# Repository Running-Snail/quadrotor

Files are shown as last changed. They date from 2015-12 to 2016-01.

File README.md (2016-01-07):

# Quadrotor
迷你四旋翼

## steps
1. 用nano板接电机，接MOFSET管，接3.7v电压，PWM测试
    1. 测试用MOFSET管（把面包线焊到三个引脚上）√ 3.7v下转动 1.13A N沟道
    2. 编写一路测试PWM（程序硬编码一个特定的百分比值）√
    3. 电池测试 √
2. 测试多路PWM和空心杯驱动（与下一步画电路板同时进行）
    1. 4路PWM驱动电机测试
    2. 电池驱动测试
    3. 蓝牙通讯（制定协议√，电脑或者手机端蓝牙传输通讯）
    4. 蓝牙协议，avr端实现 √
    5. avr端实现优化
    6. 蓝牙协议，android端实现
3. 画电路板（测试板，开发板）
    1. 初步电路√，万用板搭建实验
    2. 购买芯片（估计要买很多，以供下面的步骤使用）
    3. 焊接芯片
    4. 调试 -> 改正
4. 四旋翼结构设计
    1. 程序模拟（这个不太了解怎么模拟）
    2. 做一个模型进行测试
5. 画正式四旋翼电路板
    1. 焊接芯片
    2. 调试 -> 改正

## 蓝牙协议
接收bytes序列
序列格式

```
| pkg byte | pkg byte2 (optional) | ... | data len byte ( use 7 bits ) | data len byte 2 (optional) | ... | actual data | xor check sum |
```

```
pkgs
HELLO 0x48
SET_MOTOR 0x53
FEEDBACK 0x41
ERROR 0x45 
```

```
ERROR types
buffer_overflow 0x1
```

### SET_MOTOR 设置电机转速
设置电机1的转速为128

```
| 0x53 | 0x02 | 0x00 | 0x80 | 0xd1 |
```

### HELLO 包
```
| 0x48 | 0x0 | 0x48 | 
```

### OK 回执
```
| 0x41 | 0x2 | 0x6f | 0x6b | 0x47 |
```

## notes
* 720空心杯3.7v电压下转动 电流测得1.13A
* 笔记本usb的电流不够大，空心杯转起来了之后就没有额外的电流提供给蓝牙模块了，使用锂电池解决这个问题
* 电机转速太快的情况下会对蓝牙模块产生电磁干扰（怀疑，还需证实，需要在电机壳上加电容）
* 电路原理图
    * atmega328p最小系统
        * 晶振电路 √
        * reset按键 √
        * 电源开关 电源灯 电源插头 √
        * 稳压电路 √
        * 滤波电容 √
        * 编程/运行开关 √
        * 编程接口 √
            * 使用arduino的bootloader
                * usb转串口 外置 留出RX TX 
            * SPI下载接口 √
    * 电机电路
        * 四路PWM N沟道 MOSFET电路 √
        * 电机及外壳电容电路（减弱磁场效应）
    * 通讯模块
        * 蓝牙模块接口 √
    * 电池固定结构

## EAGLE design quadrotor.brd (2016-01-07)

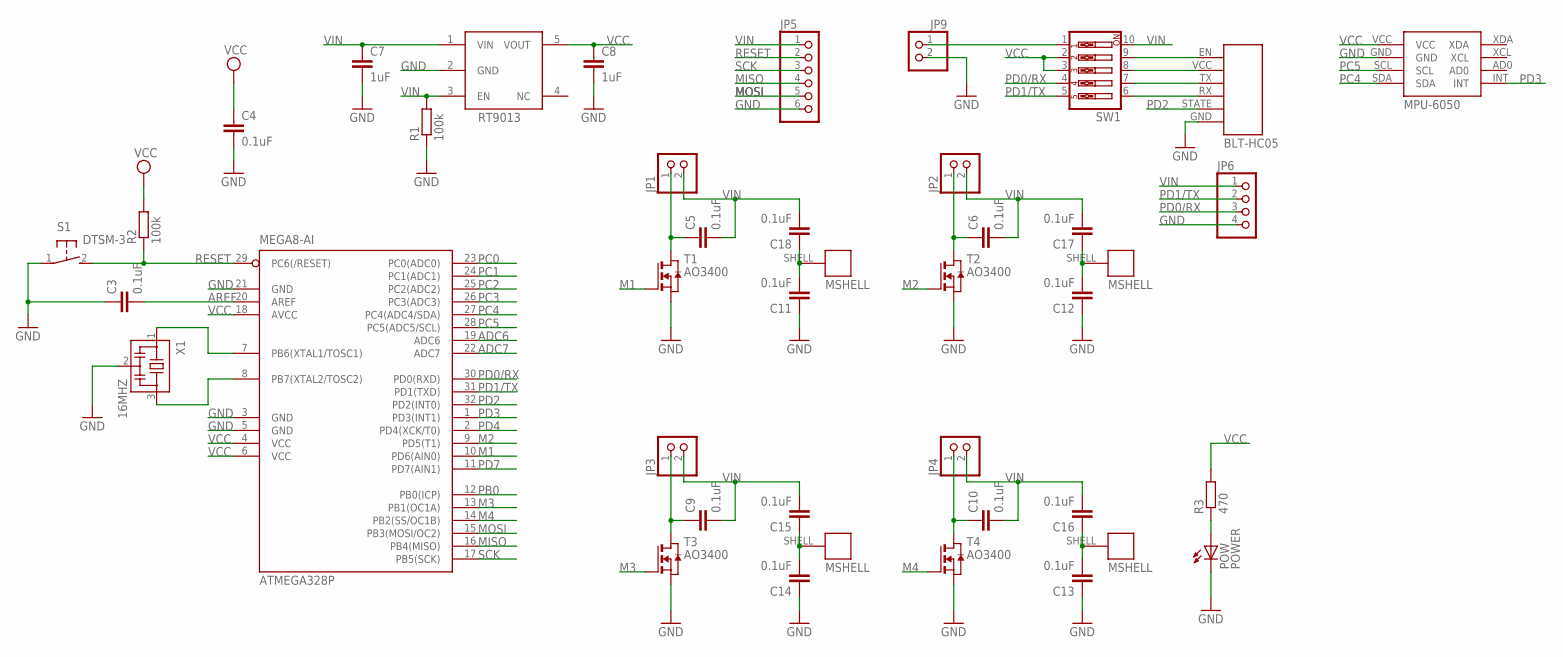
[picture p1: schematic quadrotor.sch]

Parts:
ATMEGA328P: MEGA8-AI; TQFP32-08
C3, C4, C5, C6, C9, C10, C11, C12, C13, C14, C15, C16, C17, C18: 0.1uF; C0603
C7, C8: 1uF; C0603
JP1, JP2, JP3, JP4, JP9: PINHD-1X2; 1X02
JP5: PINHD-1X6; 1X06
JP6: PINHD-1X4; 1X04
POW: POWER; LED_SML0603
R1, R2: 100k; R0603
R3: 470; R0603
S1: DTSM-3
SW1: SW_DIP-5; EDG-05
T1, T2, T3, T4: AO3400; SOT-23
U$1: RT9013; SOT-23-5
U$2: BLT-HC05
U$3, U$4, U$5, U$6: 720-MSHELL; 720MOTOR
U$7: MPU-6050
X1: 16MHZ; CSTCR6M

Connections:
ADC6: ATMEGA328P.19 (ADC6)
ADC7: ATMEGA328P.22 (ADC7)
AREF: ATMEGA328P.20 (AREF), C3.2
GND: ATMEGA328P.3 (GND), ATMEGA328P.5 (GND), ATMEGA328P.21 (GND), C3.1, C4.2, C7.2, C8.2, C11.1, C12.1, C13.1, C14.1, JP5.6, JP6.4, JP9.2, POW.C, R1.1, S1.1, T1.2 (S), T2.2 (S), T3.2 (S), T4.2 (S), U$1.2 (GND), U$2.GND, U$7.GND, X1.2
M1: ATMEGA328P.10 (PD6(AIN0)), T1.3 (G)
M2: ATMEGA328P.9 (PD5(T1)), T2.3 (G)
M3: ATMEGA328P.13 (PB1(OC1A)), T3.3 (G)
M4: ATMEGA328P.14 (PB2(SS/OC1B)), T4.3 (G)
MISO: ATMEGA328P.16 (PB4(MISO)), JP5.4
MOSI: ATMEGA328P.15 (PB3(MOSI/OC2)), JP5.5
unnamed: ATMEGA328P.7 (PB6(XTAL1/TOSC1)), X1.1
unnamed: ATMEGA328P.8 (PB7(XTAL2/TOSC2)), X1.3
unnamed: C14.2, C15.1, U$5.SHELL
unnamed: C5.1, JP1.1, T1.1 (D)
unnamed: C11.2, C18.1, U$3.SHELL
unnamed: C6.1, JP2.1, T2.1 (D)
unnamed: SW1.9, U$2.EN
unnamed: POW.A, R3.1
unnamed: C10.1, JP4.1, T4.1 (D)
unnamed: C9.1, JP3.1, T3.1 (D)
unnamed: SW1.8, U$2.VCC
unnamed: SW1.7, U$2.TX
unnamed: SW1.6, U$2.RX
unnamed: JP9.1, SW1.1
unnamed: C12.2, C17.1, U$4.SHELL
unnamed: C13.2, C16.1, U$6.SHELL
PB0: ATMEGA328P.12 (PB0(ICP))
PC0: ATMEGA328P.23 (PC0(ADC0))
PC1: ATMEGA328P.24 (PC1(ADC1))
PC2: ATMEGA328P.25 (PC2(ADC2))
PC3: ATMEGA328P.26 (PC3(ADC3))
PC4: ATMEGA328P.27 (PC4(ADC4/SDA)), U$7.SDA
PC5: ATMEGA328P.28 (PC5(ADC5/SCL)), U$7.SCL
PD0/RX: ATMEGA328P.30 (PD0(RXD)), JP6.3, SW1.4
PD1/TX: ATMEGA328P.31 (PD1(TXD)), JP6.2, SW1.5
PD2: ATMEGA328P.32 (PD2(INT0)), U$2.STATE
PD3: ATMEGA328P.1 (PD3(INT1)), U$7.INT
PD4: ATMEGA328P.2 (PD4(XCK/T0))
PD7: ATMEGA328P.11 (PD7(AIN1))
RESET: ATMEGA328P.29 (PC6(/RESET)), JP5.2, R2.1, S1.2
SCK: ATMEGA328P.17 (PB5(SCK)), JP5.3
VCC: ATMEGA328P.4 (VCC), ATMEGA328P.6 (VCC), ATMEGA328P.18 (AVCC), C4.1, C8.1, R2.2, R3.2, SW1.2, SW1.3, U$1.5 (VOUT), U$7.VCC
VIN: C5.2, C6.2, C7.1, C9.2, C10.2, C15.2, C16.2, C17.2, C18.2, JP1.2, JP2.2, JP3.2, JP4.2, JP5.1, JP6.1, R1.2, SW1.10, U$1.1 (VIN), U$1.3 (EN)

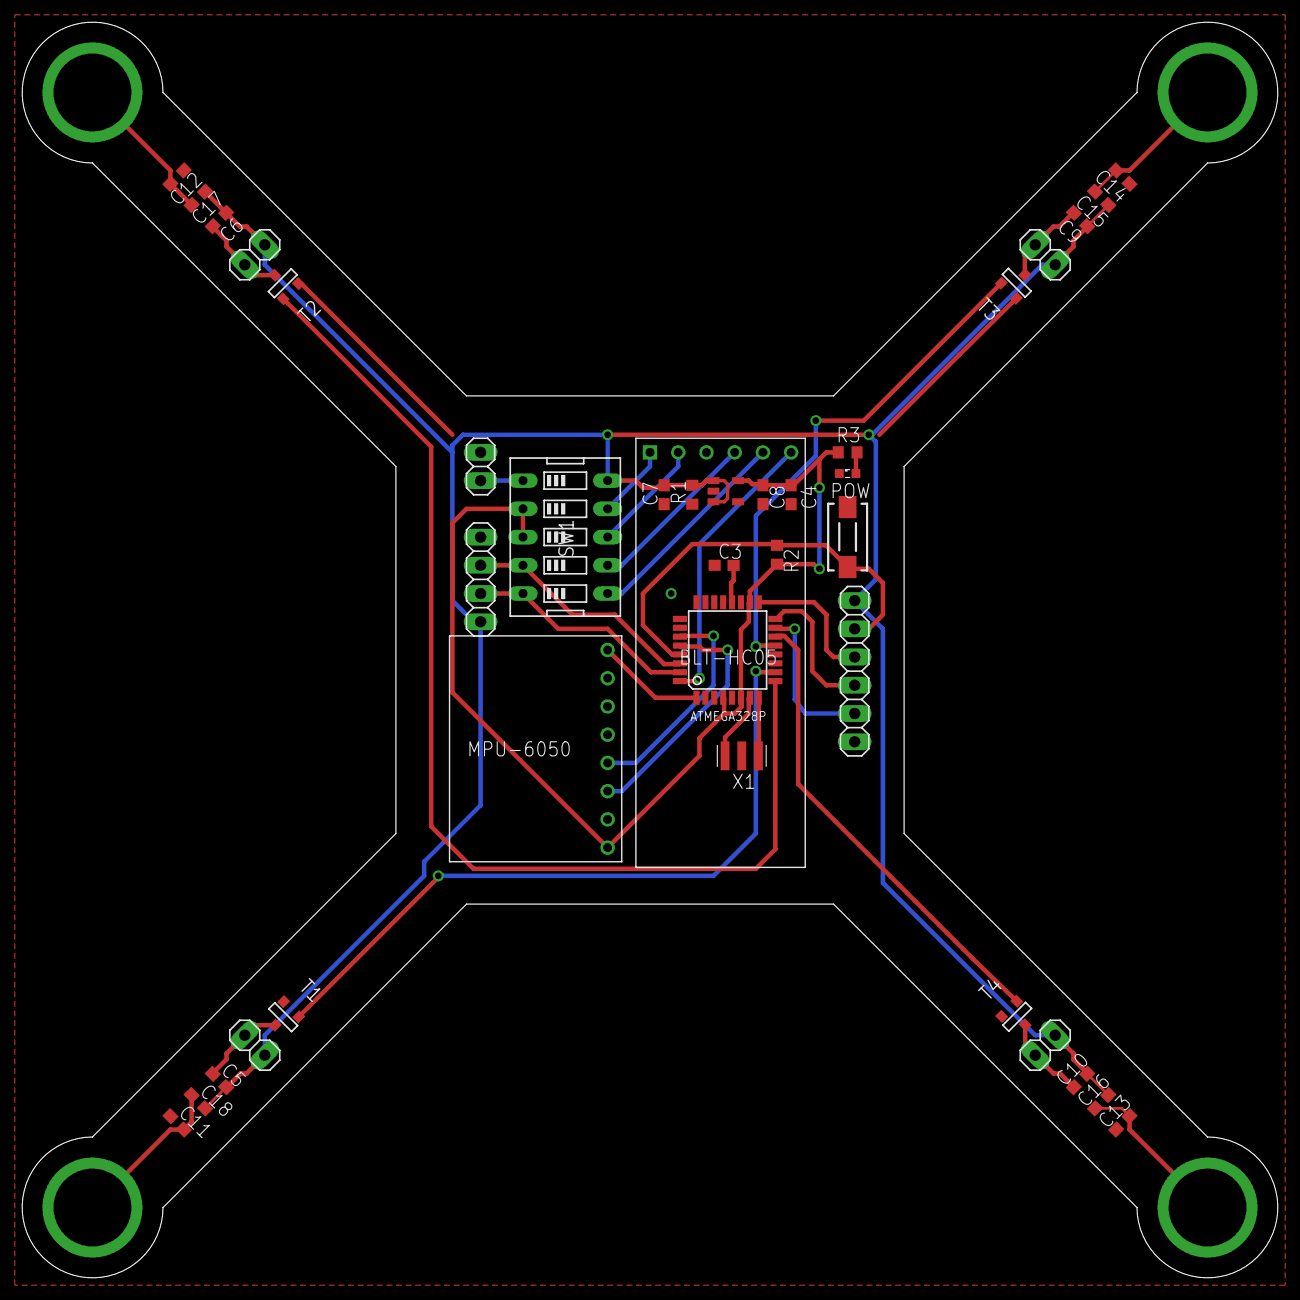
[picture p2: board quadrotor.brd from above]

Board: 2 copper layers, 113.0 x 113.0 mm, 42 parts (0 on the bottom side), 34 nets.

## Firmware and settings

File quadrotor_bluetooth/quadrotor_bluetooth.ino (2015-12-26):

#define QD_HELLO 0x48
#define QD_SET_MOTOR 0x53
#define QD_FEEDBACK 0x41
#define QD_ERROR 0x45

#define QD_PKG_LENGTH 32

#define QD_BUFFER_OVERFLOW_ERROR "\x45\x01\x01\x45"
#define QD_OK_FEEDBACK "\x41\x02\x6f\x6b\x47"
#define QD_HELLO_FEEDBACK "\x41\x05HELLO\x06"

#define QD_STATE_CMD 0
#define QD_STATE_LEN 1
#define QD_STATE_DAT 2
#define QD_STATE_CHECK 3

#define QD_MOTOR_0 OCR0A
#define QD_MOTOR_1 OCR0B
#define QD_MOTOR_2 OCR2A
#define QD_MOTOR_3 OCR2B

volatile unsigned char qd_pkg[32];
volatile unsigned int qd_pkg_top = 0;
volatile unsigned char qd_pkg_state = QD_STATE_CMD;
volatile unsigned int qd_pkg_data_len_now = 0;
volatile unsigned int qd_pkg_data_len = 0;

void qdSetMotorSpeed(unsigned char motor, unsigned char spd) {
  switch(motor) {
    case 0:
      QD_MOTOR_0 = spd;
      break;
    case 1:
      QD_MOTOR_1 = spd;
      break;
    case 2:
      QD_MOTOR_2 = spd;
      break;
    case 3:
      QD_MOTOR_3 = spd;
      break;
  }
}

void qdExecPkg() {
  switch (qd_pkg[0]) {
    case QD_HELLO:
      Serial.write(QD_HELLO_FEEDBACK);
      break;
    case QD_SET_MOTOR:
      qdSetMotorSpeed(qd_pkg[2], qd_pkg[3]);
      Serial.write(qd_pkg[3]);
      break;
  }
  qd_pkg_data_len = 0;
  qd_pkg_data_len_now = 0;
  qd_pkg_top = 0;
  qd_pkg_state = QD_STATE_CMD;
}

byte byteRead;

void setup() {
  DDRD = _BV(PD5)|_BV(PD6); // all output
  TCCR0A = 0xA3; // fast pwm
  TCCR0B = 0x2; // feq/8
  OCR0A = 0; // PD6 D6
  OCR0B = 0; // PD5 D5

  // put your setup code here, to run once:
  Serial.begin(9600);
}

void loop() {
  // put your main code here, to run repeatedly:
  if (Serial.available()) {
    byteRead = Serial.read();
    qd_pkg[qd_pkg_top] = byteRead;
    qd_pkg_top += 1;
    if (qd_pkg_top >= QD_PKG_LENGTH) {
      Serial.write(QD_BUFFER_OVERFLOW_ERROR);
    }

    switch (qd_pkg_state) {
      case QD_STATE_CMD:
        if (!(byteRead & 0x80)) qd_pkg_state = QD_STATE_LEN;
        break;
      case QD_STATE_LEN:
        qd_pkg_data_len = (qd_pkg_data_len << 8) | byteRead;
        if (!(byteRead & 0x80)) {
          if (qd_pkg_data_len == 0) {
            qd_pkg_state = QD_STATE_CHECK;
          } else {
            qd_pkg_state = QD_STATE_DAT;
          }
        }
        break;
      case QD_STATE_DAT:
        qd_pkg_data_len_now += 1;
        if (qd_pkg_data_len_now >= qd_pkg_data_len) {
          qd_pkg_state = QD_STATE_CHECK;
        }
        break;
      case QD_STATE_CHECK:
        qdExecPkg();
        break;
    }
  }
}

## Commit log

2015-12-26 done bluetooth protocal
    [quadrotor.brd, quadrotor.sch]
2015-12-26 remove track backup files
2015-12-27 mostly done layout and is routing now
    [quadrotor.brd, quadrotor.sch]
2015-12-29 basically done pcb layout
    [quadrotor.brd, quadrotor.sch]
2016-01-07 basically done v1 brd
    [quadrotor.brd, quadrotor.sch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]
